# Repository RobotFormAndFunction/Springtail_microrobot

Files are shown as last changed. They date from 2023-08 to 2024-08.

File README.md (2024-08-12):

# Springtail jumping microrobot
This GitHub repository describes the mechanical and electrical hardware and software for an autonomous spring-tail inspired jumping microrobot. 

To cite:
```bibtex
@INPROCEEDINGS{Singh2024,
  author={Singh, Shashwat and Temel, Zeynep and St.~Pierre, Ryan},
  booktitle={2024 IEEE International Conference on Robotics and Automation (ICRA)}, 
  title={Multi-modal jumping and crawling in an autonomous, springtail-inspired microrobot}, 
  year={2024},
  volume={},
  number={},
  pages={5999-6005},
  doi={10.1109/ICRA57147.2024.10610130}}
```

https://github.com/RobotFormAndFunction/Springtail_microrobot/assets/98366383/b097e502-10c7-4643-9109-868a8b8baddd

# Hardware Specifications
This section details the electrical and mechanical hardware used in the jumping microrobot.

## Electrical hardware
The custom PCB for the jumping microrobot is detailed in [here](https://github.com/RobotFormAndFunction/Springtail_microrobot/tree/main/Electrical%20Hardware), with the schematic of the board and Gerber files. The microcontroller is an ATtiny10 which is a small, low-power 8-bit AVR RISC-based microcontroller with 1 KB ISP Flash memory, 32B SRAM, four general purpose I/O lines. The summary of electrical hardware is below in the BOM. 

<details><summary>Bill of materials (BOM)</summary>

#### BOM

| Component | Value	| Quantity | Package size |
| :--- | --- | :---: | --- |
| Capacitor |	0.1 µF |	2 |	0603 |
| Resistor |	2 kΩ |	1 |	0603 |
| Motor driver |	DRV8835 |	1 |	12-WSON |
| MCU |	ATtiny10 |	1 |	SOT-23-6 |

</details>

## Mechanical hardware
The files required for cutting the spring tail is [here](https://github.com/RobotFormAndFunction/Springtail_microrobot/tree/main/Mechanical%20Hardware). Other mechanical components are listed in the BOM in the mechanical hardware, along with a video of assembly.

# Software specification
The microrobot software was written in Embedded C using PlatformIO and programmed with the Tiny Programming Interface from Atmel using the Atmel-ICE. The source code is available [here](https://github.com/RobotFormAndFunction/Springtail_microrobot/tree/main/Software)

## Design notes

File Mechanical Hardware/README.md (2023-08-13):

# Mechanical hardware
The files required for cutting the spring tail is [here](https://github.com/RobotFormAndFunction/Springtail_microrobot/blob/main/Mechanical%20Hardware/jumper_design.dxf). Other mechanical components are listed in the BOM.

<summary>Bill of materials (BOM)</summary>

#### BOM

| Component | Quantity	| Comments |
| :--- | :---: | --- |
| Tail | 1 | Cut with jumper_design.dxf from 0.19 Super elastic SMA |
| Legs |	4 |	Leads from through hole resistors |
| Actuator |	1 |	Hinge actuator from https://micronwings.com/product/actuator-set-hinge-with-leads-and-connectors/ |

## Assembly
A video of the assembly of the robot is shown below

https://github.com/RobotFormAndFunction/Springtail_microrobot/assets/98366383/454ca516-8a3c-4a6f-8e5d-e53803f9ef20

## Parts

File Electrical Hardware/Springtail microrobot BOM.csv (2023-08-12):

ID | Name | Designator | Footprint | Quantity | Manufacturer Part | Manufacturer | Supplier | Supplier Part | Price
1 | 0.1u | C1 | C0201 | 1 | C0201C0G1R6B500NTA | EYANG(宇阳科技) | LCSC | C124768
2 | KH-1.27PH180-1X2P-L7.2 | H1,H2,H3,H4 | HDR-TH_2P-P1.27-V-M | 4 | KH-1.27PH180-1X2P-L7.2 | kinghelm(金航标) | LCSC | C2938400 | 0.015
3 | 10k | R1 | R0201 | 1 | 0201WMJ0201TEE | UNI-ROYAL(厚声) | LCSC | C473442 | 0.001
4 | 2k | R2 | R0201 | 1 | 0201WMJ0201TEE | UNI-ROYAL(厚声) | LCSC | C473442 | 0.001
5 | ATTINY10-TSHR | U1 | SOT-23-6_L2.9-W1.6-P0.95-LS2.8-BR | 1 | ATTINY10-TSHR | MICROCHIP | LCSC | C128438 | 0.735
6 | EAPST1608A0 | U2 | D0603-RD | 1 | EAPST1608A0 | Everlight | Mouser | 638-EAPST1608A0
7 | DRV8838DSGR | U3 | WSON-8_L2.0-W2.0-P0.50-TL-EP | 1 | DRV8838DSGR | TI(德州仪器) | LCSC | C86667 | 1.747

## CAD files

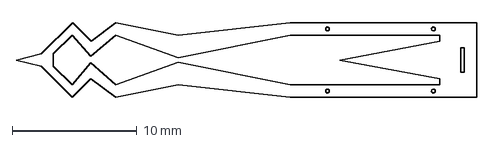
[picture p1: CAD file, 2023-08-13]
Mechanical Hardware/jumper_design.dxf
37.0 x 6.00 mm

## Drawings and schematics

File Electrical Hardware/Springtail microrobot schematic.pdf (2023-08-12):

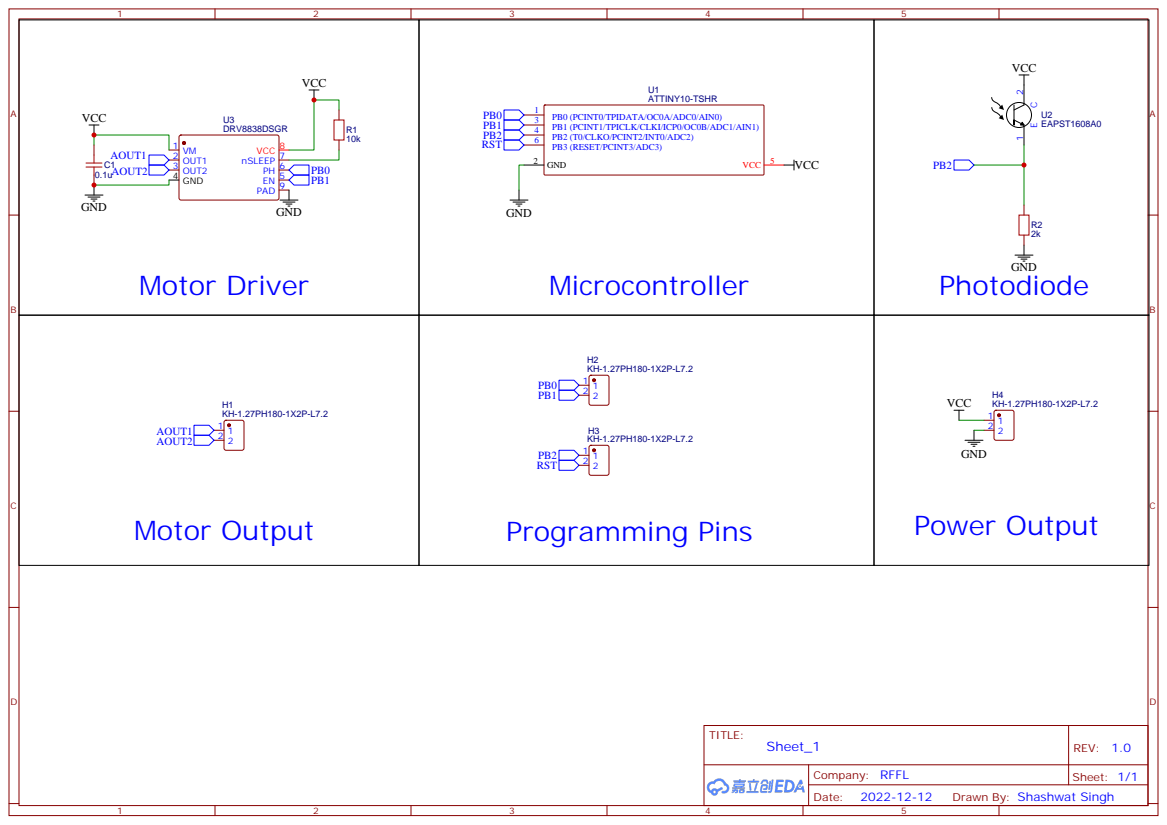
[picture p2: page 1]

Drawn By: Shashwat Singh

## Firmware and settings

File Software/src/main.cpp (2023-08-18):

#include <avr/io.h>
#include <avr/interrupt.h>
#include <util/delay.h>

int main() {
	DDRB = (1<<DDB0) | (1<<DDB1) ;          // set PB0 & PB1 as output
	
	ADMUX = (1<<MUX1) | (0<<MUX0);		//Select ADC2
	ADCSRA = (1<<ADEN) | (ADPS2);		//Set ADC2 analog pin on PB2
	
	
	while (1) {
		
		int val;
		ADCSRA = ADCSRA | (1<<ADSC);
		while (ADCSRA & (1<<ADSC));
		
		val = ADCL; //store the value from the ADC
		
		if (val>70){
			
			PORTB |= (1<<PORTB0);   // drive PD1 high
			PORTB &= ~(1<<PORTB1);
			_delay_ms(12.5);         // delay 12.5 ms
			PORTB |= (1<<PORTB1);
			PORTB &= ~(1<<PORTB0);  // drive PD1 low
			_delay_ms(12.5);         // delay 12.5 ms
			
		}			
			
		}
		
	}
